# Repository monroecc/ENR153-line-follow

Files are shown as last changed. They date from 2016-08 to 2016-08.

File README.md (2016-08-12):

A simple arduino sketch to control a car (car.jpg) as it drives around a track.

control_board
--------------
Contains control board schematic files, parts list, users manual, and LaTex source files.

pid_info
--------
Contains a basic introduction to PID control and PID tuning instructions. This is a good starting point for anyone wanting to tune the PID values if the current ones aren't working out.

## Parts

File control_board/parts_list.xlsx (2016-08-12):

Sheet: Sheet1
 |  |  |  |  |  | Number of Boards: |  |  |  | 36
Parts | Website | Function | COST/unit | QTY(per board) | Cost/Board | QTY for 36 Boards | Less current inventory(not complete) | Adjusted qty | COST for 36 Boards |  | Components We may need but already have
Switch | http://www.digikey.com/product-detail/en/e-switch/500SSP1S2M2QEA/EG5137-ND/1803993 | Digital Switches | $2.61 | 3.00 | $7.83 | 108 | 0 | 108 | $281.88 |  | Wire
Header Pins(40) | http://www.digikey.com/product-detail/en/sullins-connector-solutions/PRPC040SFAN-RC/S1211EC-40-ND/2775334 | Interface with arduino and other components | $0.75 | 2.00 | $1.50 | 72 | 0 | 72 | $54.00 |  | Solder
LED's | http://www.digikey.com/product-search/en?mpart=LTL-4236N&vendor=160 | State indicator | $0.26 | 3.00 | $0.78 | 108 | 0 | 108 | $28.08 |  | Resistors
10 LED Bar | http://www.digikey.com/product-detail/en/lite-on-inc/LTA-1000G/160-1067-ND/153278 | Indicate Which sensors on line array are seeing the line | $1.30 | 1.00 | $1.30 | 36 | 0 | 36 | $46.80
QRT-8 reflectance Sensor | https://www.pololu.com/product/960 | To follow the line | $7.95 | 1.00 | $7.95 | 36 | 0 | 36 | $286.20
16 pin connector for QRT-8 | http://www.digikey.com/product-detail/en/on-shore-technology-inc/302-R161/ED10535-ND/2794246 | Connect the qrt8 sensor to the board (HEADER) | $0.42 | 1.00 | $0.42 | 36 | 0 | 36 | $15.01
16 pin (8x2) ribbon cable - 5ft | http://www.digikey.com/product-detail/en/assmann-wsw-components/AWG28-16-G-1-300-R/AE16A-5-ND/2272545 | Connect the qrt8 sensor to the board (CABLE) | $4.38 | 0.15 | $0.66 | 5.4 | 0 | 5.4 | $23.66
DCCduino uno r3 | http://www.newegg.com/Product/Product.aspx?Item=9SIA5W02EF6926 | Conroller Board - arduino uno r3 clone | $8.49 | 1.00 | $8.49 | 36 | 0 | 36 | $305.64
Connection Terminal | http://www.mouser.com/ProductDetail/TE-Connectivity/41729/?qs=EkXmzH7ytS4F3wZMq8AwJw%3D%3D | Connect board to motors | $0.23 | 2.00 | $0.46 | 72 | 0 | 72 | $16.49
9v Connector | http://www.digikey.com/product-detail/en/mpd-memory-protection-devices/BS6I-MC/BS6I-MC-ND/252231 | Connect Battery back to board | $0.69 | 1.00 | $0.69 | 36 | 36 | 0 | $0.00
5v Regulator | http://www.digikey.com/product-detail/en/fairchild-semiconductor/LM7805CT/LM7805CT-ND/458698 | Regulate voltage for arduino and servo | $0.53 | 1.00 | $0.53 | 36 | 36 | 0 | $0.00
 |  | TOTAL |  | One Board | $30.60 |  |  | For 36 Boards | $1057.76
Other Considerations
Parts | Website | consideration | COST/unit
atmega328p | http://www.digikey.com/product-detail/en/atmel/ATMEGA328P-PU/ATMEGA328P-PU-ND/1914589 | replacement microcontroller for ARDUINO uno R3, the microcontroller on the DCCduino uno can't be replaced | $3.03
arduino uno | http://www.robotshop.com/en/arduino-uno-usb-microcontroller-rev-3.html | The micro controller can be replaced, price above | $18.78
DCCduino | http://www.newegg.com/Product/Product.aspx?Item=9SIA5W02EF6926 | The micro controller can't be replaced | $8.49

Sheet: Sheet2
 |  |  |  |  |  |  |  |  | Number of Boards: |  |  |  | 100
Part | Value | Link | vendor | Part# | Function | COST/unit | QTY/Car | Cost/Car | QTY for 100 Boards | Less current inventory #(not complete)# | Adjusted qty | COST for 100 Boards |  | Components We may need but already have
Clock and Capacitors | 16MHz 18p | https://www.adafruit.com/product/2215 | DigiKey | 399-9760-ND | Provide Clock for ATMega Chip | $0.15 | 1.00 | $0.15 | 100 | 0 | 100 | $14.85 |  | Solder
Capacitor | .1u | http://www.digikey.com/product-detail/en/avx-corporation/SR215E104MAR/478-3193-ND/936835 | DigiKey | 478-3193-ND | Signal Handling | $0.14 | 3.00 | $0.41 | 300 | 0 | 300 | $41.40 |  | Flux
Capacitor | .22u | http://www.digikey.com/product-detail/en/avx-corporation/SR211E224ZAR/478-3191-ND/936833 | DigiKey | 478-3191-ND | Signal Handling | $0.17 | 1.00 | $0.17 | 100 | 0 | 100 | $16.79 |  | Multimeter
Diode | - | http://www.digikey.com/product-detail/en/fairchild-semiconductor/1N914BTR/1N914BCT-ND/458919 | DigiKey | 1N914BCT-ND | Reset Switch (See Arduino Eagle Schmatic) | $0.03 | 1.00 | $0.03 | 100 | 0 | 100 | $3.32 |  | Arduino Uno Board (1-3)
LED | - | http://www.digikey.com/product-detail/en/kingbright/WP113IDT/754-1201-ND/1747600 | DigiKey | 754-1201-ND | Indicator | $0.03 | 3.00 | $0.10 | 300 | 0 | 300 | $9.96
Switch | 4A | http://www.digikey.com/product-detail/en/e-switch/500SSP1S2M2QEA/EG5137-ND/1803993 | DigiKey | EG5137-ND | Control Volage | $2.11 | 3.00 | $6.33 | 300 | 0 | 300 | $632.70
Switch | <1A | http://www.digikey.com/product-detail/en/c-k-components/OS102011MS2QS1/CKN9542-ND/1981413 | DigiKey | CKN9542-ND | Control Volage | $0.33 | 3.00 | $0.99 | 300 | 0 | 300 | $99.46
Transistor | 2N3904 | http://www.digikey.com/product-detail/en/atmel/ATMEGA328P-PU/ATMEGA328P-PU-ND/1914589 | DigiKey | 2N3904FS-ND | Multiplex bar led output and Line sensor input | $0.09 | 1.00 | $0.09 | 100 | 0 | 100 | $9.01
Atmega Socket | 28 Pin | https://www.sparkfun.com/products/7942 | SparkFun | PRT-07942 | Holds ATMega chip, easy to replace | $0.95 | 1.00 | $0.95 | 100 | 0 | 100 | $95.00
LED Bar | 10 Segment | http://www.digikey.com/product-search/en?mpart=DC7G3HWA&vendor=754 | DigiKey | 754-1671-5-ND | Calibration and line sensor evaluation | $1.12 | 1.00 | $1.12 | 100 | 0 | 100 | $112.00
Male Pin Header | 40 Pin | https://www.sparkfun.com/products/116 | SparkFun | PRT-00116 | Misc | $1.50 | 0.33 | $0.49 | 32.5 | 0 | 32.5 | $48.75
9V Battery Clip | - | http://www.digikey.com/product-detail/en/mpd-memory-protection-devices/BS6I-MC/BS6I-MC-ND/252231 | DigiKey | BS6I-MC-ND | Connect to main power | $0.62 | 1.00 | $0.62 | 100 | 0 | 100 | $62.00
5V Regulator | LM7805 | http://www.digikey.com/product-detail/en/fairchild-semiconductor/LM7805CT/LM7805CT-ND/458698 | DigiKey | LM7805CT-ND | Provide ATMega and servo with proper votage | $0.40 | 1.00 | $0.40 | 100 | 0 | 100 | $39.65
Reflectance Sensor | QRT-8 | https://www.pololu.com/product/960 | Pololu | QTR-8A-960 | Input for line following | $6.95 | 1.00 | $6.95 | 100 | 0 | 100 | $695.00
16 Pin Angle Leads | - | http://www.digikey.com/product-detail/en/on-shore-technology-inc/302-R161/ED10535-ND/2794246 | DigiKey | ED10535-ND | Connect line sensor to board | $0.42 | 1.00 | $0.42 | 100 | 0 | 100 | $41.70
16 Pin Ribbon Cable | - | http://www.digikey.com/product-detail/en/assmann-wsw-components/AWG28-16-G-1-300-R/AE16A-5-ND/2272545 | DigiKey | AE16A-5-ND | Connect line sensor to board | $4.38 | 1.00 | $4.38 | 100 | 0 | 100 | $438.20
Reset Button | - | http://www.digikey.com/product-detail/en/cw-industries/GPTS203212B/CW182-ND/3190592 | DigiKey | CW182-ND | Reset ATMega chip | $0.61 | 1.00 | $0.61 | 100 | 0 | 100 | $61.05
 |  |  |  |  | TOTAL |  | One Board | $12.88 |  |  | For 100 Boards | $2420.84
 |  |  |  |  |  |  | One Car | $24.21
One Time Purchases
AVR Pocket Programmer | - | https://www.sparkfun.com/products/9825 | Sparkfun | PGM-09825 | Burn Bootloader | $14.95 | 2.00 | $29.90
FTDI CABLE | - | https://www.sparkfun.com/products/9718 | Sparkfun | DEV-09718 | Upload To Board | $17.95 | 2.00 | $35.90
 |  |  |  |  | TOTAL |  |  | $65.80
NOTE: | The ribbon cables are cheaper in bulk, but they must be assbled at MCC

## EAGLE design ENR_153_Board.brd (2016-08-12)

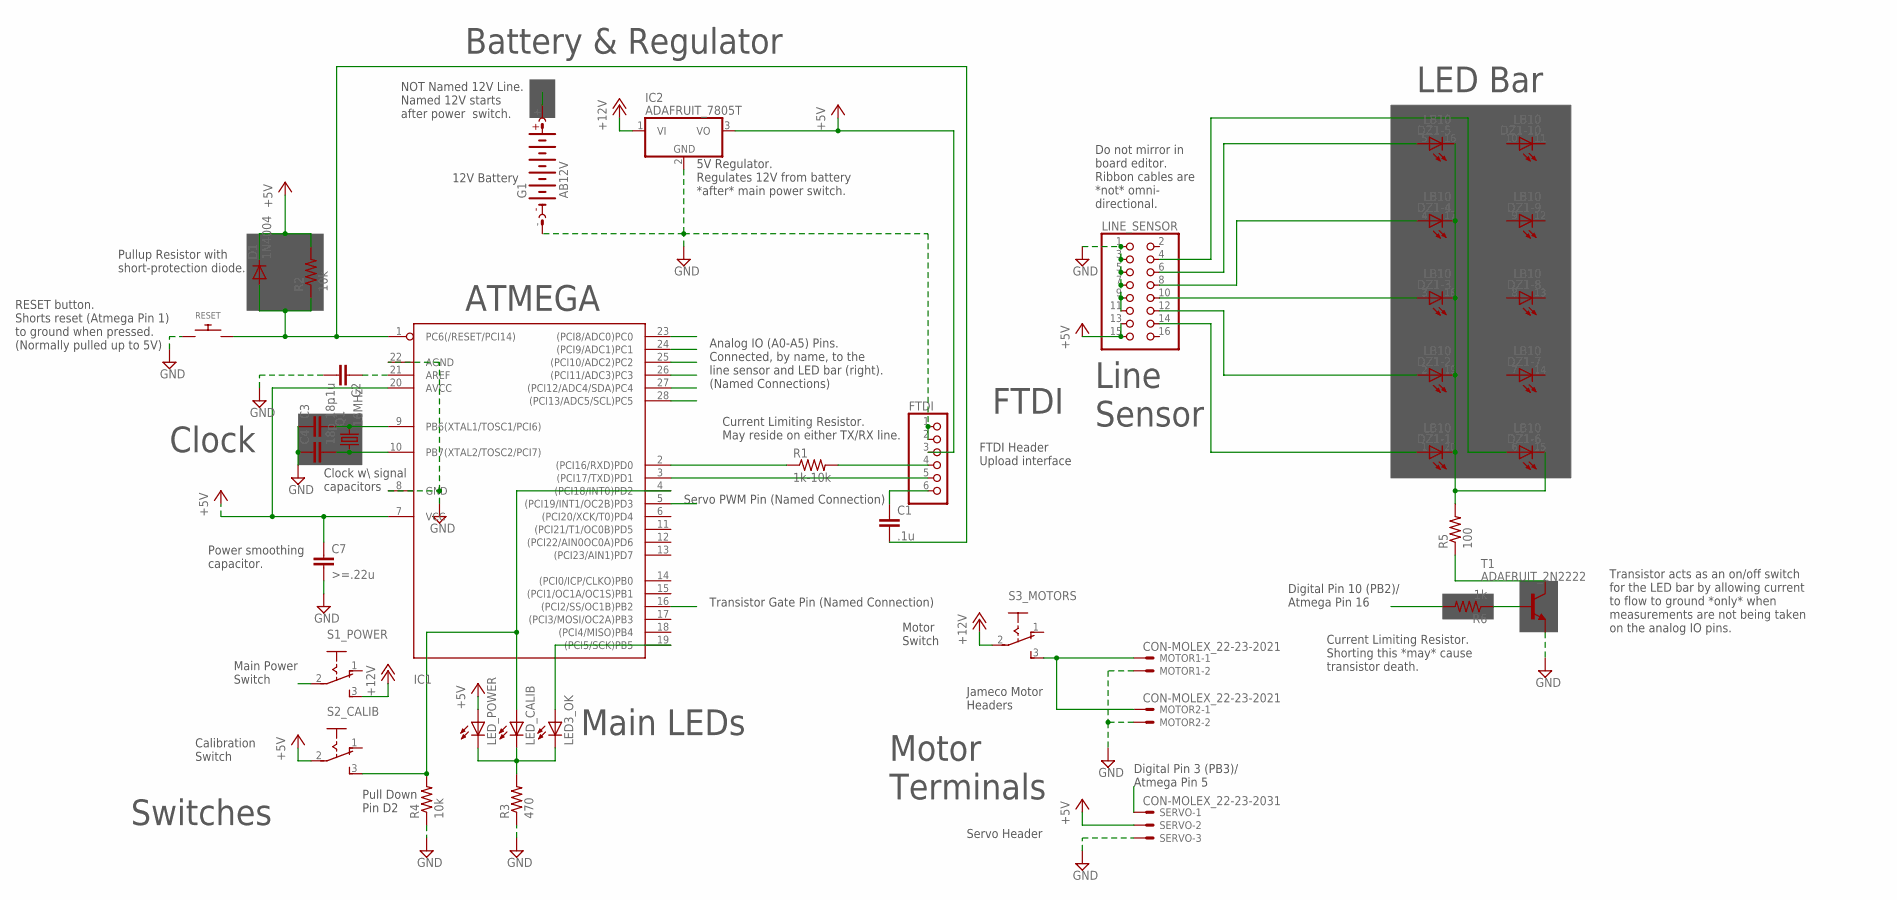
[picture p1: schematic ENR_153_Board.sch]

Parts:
C1, C2: .1u; CAPACITOR-WIMA_C5B3
C3, C4: 18p; CAPACITOR-WIMA_C5B3
C7: >=.22u; CAPACITOR-WIMA_C5B3
D1: 1N4004; DIODE_DO35-7
DZ1: LB10
FTDI: PINHD-1X6; 1X06
G1: AB12V; BATTERY_AB9V
IC1: ATMEGA168V-10P; DIL28-3
IC2: ADAFRUIT_7805T; ADAFRUIT_TO220H
LED3_OK: ADAFRUIT_LEDSQR2X5; ADAFRUIT_LED2X5
LED_CALIB: ADAFRUIT_LEDSQR2X5; ADAFRUIT_LED2X5
LED_POWER: ADAFRUIT_LEDSQR2X5; ADAFRUIT_LED2X5
LINE_SENSOR: PINHEAD_PINHD-2X8; PINHEAD_2X08
MOTOR1, MOTOR2: CON-MOLEX_22-23-2021
Q1: 16MHz; ADAFRUIT_HC49/S
R1: 1k-10k; ADAFRUIT_0207/7
R2, R4: 10k; ADAFRUIT_0207/7
R3: 470; ADAFRUIT_0207/7
R5: 100; ADAFRUIT_0207/7
R6: 1k; ADAFRUIT_0207/7
RESET: ADAFRUIT_SWITCH_PUSHBUTTONEVQ-PE; ADAFRUIT_TACT_PANA-EVQ
S1_POWER, S2_CALIB, S3_MOTORS: SWITCH_255SB
SERVO: CON-MOLEX_22-23-2031
T1: ADAFRUIT_2N2222; ADAFRUIT_TO92-EBC-OVAL

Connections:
+5V: C7.1, D1.C, FTDI.3, IC1.7 (VCC), IC1.20 (AVCC), IC2.3 (VO), LED_POWER.A, LINE_SENSOR.13, LINE_SENSOR.15, R2.2, S2_CALIB.2, SERVO.2
+12V: IC2.1 (VI), S1_POWER.3 (S), S3_MOTORS.2
A0: DZ1.6 (A), IC1.23 ((PCI8/ADC0)PC0), LINE_SENSOR.4
A1: DZ1.5 (A), IC1.24 ((PCI9/ADC1)PC1), LINE_SENSOR.6
A2: DZ1.4 (A), IC1.25 ((PCI10/ADC2)PC2), LINE_SENSOR.8
A3: DZ1.3 (A), IC1.26 ((PCI11/ADC3)PC3), LINE_SENSOR.10
A4: DZ1.2 (A), IC1.27 ((PCI12/ADC4/SDA)PC4), LINE_SENSOR.12
A5: DZ1.1 (A), IC1.28 ((PCI13/ADC5/SCL)PC5), LINE_SENSOR.14
GND: C2.2, C3.1, C4.1, C7.2, FTDI.1, FTDI.2, G1.-, IC1.8 (GND), IC1.22 (AGND), IC2.2 (GND), LINE_SENSOR.1, LINE_SENSOR.3, LINE_SENSOR.5, LINE_SENSOR.7, LINE_SENSOR.9, LINE_SENSOR.11, MOTOR1.2, MOTOR2.2, R3.1, R4.1, RESET.P$1, SERVO.3, T1.E
MAINS: G1.+, S1_POWER.2
unnamed: C1.2, D1.A, IC1.1 (PC6(/RESET/PCI14)), R2.1, RESET.P$2
unnamed: R5.1, T1.C
unnamed: FTDI.4, R1.2
unnamed: C1.1, FTDI.6
unnamed: IC1.2 ((PCI16/RXD)PD0), R1.1
unnamed: FTDI.5, IC1.3 ((PCI17/TXD)PD1)
unnamed: C2.1, IC1.21 (AREF)
unnamed: IC1.19 ((PCI5/SCK)PB5), LED3_OK.A
unnamed: LED3_OK.K (C), LED_CALIB.K (C), LED_POWER.K (C), R3.2
unnamed: C3.2, IC1.9 (PB6(XTAL1/TOSC1/PCI6)), Q1.2
unnamed: C4.2, IC1.10 (PB7(XTAL2/TOSC2/PCI7)), Q1.1
unnamed: R6.1, T1.B
unnamed: DZ1.15 (C), DZ1.16 (C), DZ1.17 (C), DZ1.18 (C), DZ1.19 (C), DZ1.20 (C), R5.2
unnamed: IC1.4 ((PCI18/INT0)PD2), LED_CALIB.A, R4.2, S2_CALIB.3 (S)
unnamed: MOTOR1.1, MOTOR2.1, S3_MOTORS.3 (S)
SERVO: IC1.5 ((PCI19/INT1/OC2B)PD3), SERVO.1
TRANSISTOR_GATE: IC1.16 ((PCI2/SS/OC1B)PB2), R6.2

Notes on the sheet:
Current Limiting Resistor. May reside on either TX/RX line.
Analog IO (A0-A5) Pins. Connected, by name, to the line sensor and LED bar (right). (Named Connections)
5V Regulator. Regulates 12V from battery *after* main power switch.
Servo Header
Jameco Motor Headers
Main Power Switch
Motor Switch
Calibration Switch
Pull Down Pin D2
LED Bar
ATMEGA
FTDI Header Upload interface
12V Battery
NOT Named 12V Line. Named 12V starts after power switch.
Power smoothing capacitor.
Current Limiting Resistor. Shorting this *may* cause transistor death.
Transistor acts as an on/off switch for the LED bar by allowing current to flow to ground *only* when measurements are not being taken on the analog IO pins.
Do not mirror in board editor. Ribbon cables are *not* omni- directional.
Digital Pin 10 (PB2)/ Atmega Pin 16
Transistor Gate Pin (Named Connection)
Servo PWM Pin (Named Connection)
Digital Pin 3 (PB3)/ Atmega Pin 5
Clock w\ signal capacitors
Pullup Resistor with short-protection diode.
RESET button. Shorts reset (Atmega Pin 1) to ground when pressed. (Normally pulled up to 5V)
Clock
Main LEDs
Switches
Line Sensor
Battery & Regulator
FTDI
Motor Terminals

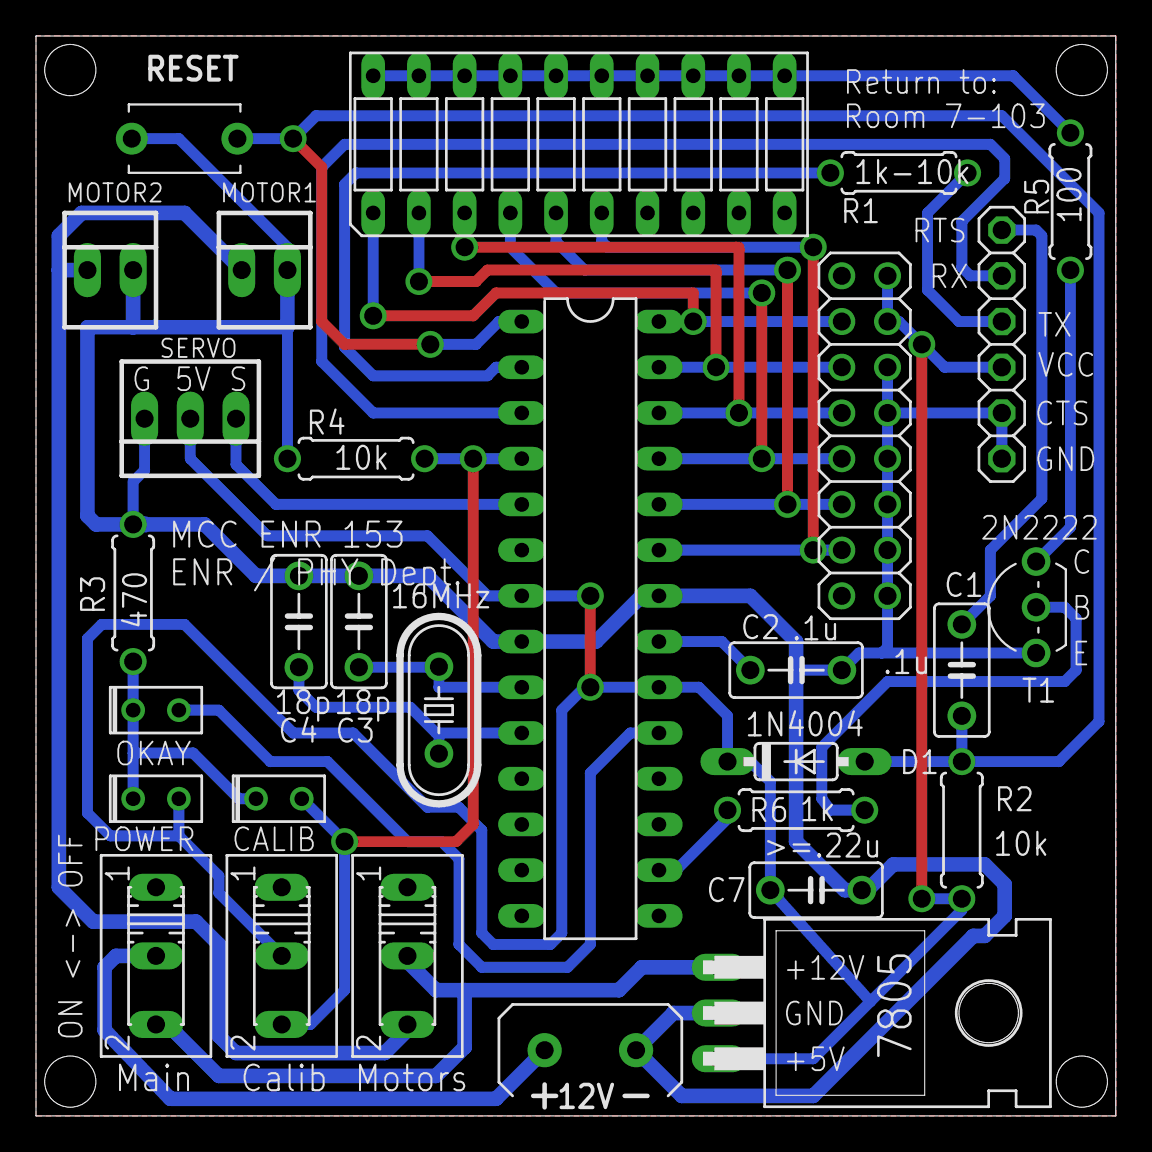
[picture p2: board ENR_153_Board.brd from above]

Board: 2 copper layers, 60.0 x 60.0 mm, 30 parts (0 on the bottom side), 27 nets.

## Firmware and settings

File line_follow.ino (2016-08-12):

#include <Servo.h>
#include "control.h"

line l;
long adjust = 5;
Servo steer;

int s_cal, state;

analog_sensor sensors[NUM_A_SENSORS];
int pin_map[NUM_A_SENSORS] = {A0, A1, A2, A3, A4, A5}; //Just incase we want to reverse the order, or in the event of a redesign adjacent sensors don't need to map to adjacent analog pins.

void setup() {
  Serial.begin(9600);
  state = -1;
  s_cal = 0;

  for (int i = 0; i < NUM_A_SENSORS; i++)
  {
    sensors[i].init(pin_map[i]);
  }

  l.init(sensors, NUM_A_SENSORS, &adjust);

  l.load();

  steer.attach(SERVO_PIN);

  pinMode(ANALOG_TRANSISTOR_PIN, OUTPUT);
  digitalWrite(ANALOG_TRANSISTOR_PIN, LOW);
}


void loop() {

  if ((millis() % 100) < 5) //Only check every 100ms. Makes loop faster assuming digitalRead() is slower than logical condition
    s_cal = digitalRead(CALIBRATE_PIN);

  switch (state)
  {
    case 0:
      l.follow();
      adjust = constrain(adjust, MAX_ADJ_RIGHT, MAX_ADJ_LEFT);
      steer.write(SERVO_CENTER - adjust);
      state = s_cal;
      break;
    case 1:
      l.clear_calibration();
      steer.write(SERVO_CENTER);
      state = 2;
      break;
    case 2:
      l.calibrate();
      display_line(l);
      if (s_cal == LOW)
        state = 3;
      break;
    case 3:
      l.save();
      state = 0;
      break;
    default:
      state = 0;
  }
}

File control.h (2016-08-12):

#ifndef CONTROL
    #define CONTROL

    #include "definitions.h"

    //#define DEBUG       // Uncommenting this line prints the binary representation of the line sensor to the console during calibration
    //#define DEBUG_EACH  // Uncommenting this line prints the min and max line sensor values to the console during calibration

    #ifdef DEBUG
        #include "toolbox.h" //debug tools
    #endif

    #define NUM_A_SENSORS 6             // Number of analog sensors, used as array length
    #define CALIBRATE_PIN 2             // Connected to the calibration pin
    #define ANALOG_TRANSISTOR_PIN 10    // Pin connected to the transistor base, used to cut the bar led out of the line follow circuit
    #define SERVO_PIN 3                 // Servo is connected to this pin, it is a PWM pin
    
    #include <Arduino.h>
    #include <EEPROMex.h> //Make sure you install this via the Arduino IDE, allows writing of things other than bytes

    //GENERAL PID
    class PID
    {
    public:
        float pidd[4]; //err, last error, running integral, adjust
        float w[3];    //holds pid constants

        float circ_i[I_BUFFER_LEN]; // only worry about summing the last 30 terms of remond sum
        int head;         // head for circuilar array

        void set_pid(float p, float i, float d)
        {
            w[0] = p;w[1] = i;w[2] = d;
            pidd[0] = 0; pidd[1] = 0; pidd[2] = 0;
            head = 0;

            memset(circ_i, 0x00, sizeof(float)*I_BUFFER_LEN);
        }

        float slice(float err)
        {
            pidd[1] = pidd[0];                      // set last err pidd[1]
            pidd[0] = err;                          // set current err pidd[0]

            //The integral term only takes into account the last I_BUFFER_LEN readings. It only sums these readings when the car is moving away from the line. When moving towards the line the integral term is set to zero along with the circular buffer.
            if( abs(pidd[0]) > abs(pidd[1]) ){
                pidd[2] -= circ_i[head];                // Subract off the element of circ_i you are about to replace
                circ_i[head] = (pidd[0] + pidd[1])/2;   // Set the element of the cirular array to this "slice" of the integral
                pidd[2] += circ_i[head];                // Add to integral element pidd[2]
                head++;                                 // increments head

                if(head == I_BUFFER_LEN)
                    head = 0; //wrap around

            }else if(circ_i[head] != 0.0){
                //only clear the buffer once, readings of zero pretty much never happen
                pidd[2] = 0;
                memset(circ_i, 0x00, sizeof(float)*I_BUFFER_LEN); // clear buffer
            }                             


            pidd[3] = pidd[0]*w[0] + pidd[2]*w[1] + (pidd[0] - pidd[1]) * w[2]; // Compute PID output and save it in pidd[3]

            return pidd[3];                                                     // return adjustment
        }
    };

    class analog_sensor
    {
    public:
        int pin, min, max; //analog pin [0, 5], absolute min for this sensor, absolute max for this sensor
        float scale;      // Scale value, used to fit any reading to a value between 0-100 (normalize sensor)
        static int eeprom_head; // The current eeprom position, keeps sensors from overwriting each others calibration
        void init(int arg_pin)
        {
            this->pin = arg_pin;
            this->scale = 1.0;
            this->min = 2000;
            this->max = 0;
        }

        int read_sensor()
        {
            // Nomalize sensor, contrain, and return
            int ret = (int)((analogRead(pin) - min)*scale); //calculate normalized sensor value
            ret = constrain(ret, 0, 100);
            return ret;
        }

        void calibrate_point()
        {
            int cal = analogRead(pin);
            if(cal < min){
                min = cal; // Set new absolute min
            }
            else if(cal > max){
                max = cal;  // Set new absolute max
            }
            scale = 100.0/(max - min);  // Compute scale
        }

        static void reset_head()
        {
            analog_sensor::eeprom_head = EEPROM_OFF;
        }

        void reset_calibration()
        {
            this->scale = 1.0;
            this->min = 1025;
            this->max = 0;
        }

        void save() //save cailbration (min, max) for this sensor
        {
            EEPROM.writeInt(eeprom_head, min);
            eeprom_head += sizeof(int);
            EEPROM.writeInt(eeprom_head, max);
            eeprom_head += sizeof(int);
        }

        void load() //load calibration for this sensor
        {
            min = EEPROM.readInt(eeprom_head);
            eeprom_head += sizeof(int);
            max = EEPROM.readInt(eeprom_head);
            eeprom_head += sizeof(int);

            scale = 100.0/(max - min);
        }
    };

    int analog_sensor::eeprom_head = 0;

    class line
    {
    private:
        analog_sensor * sensors;    // Array of sensors to compute line position from
        PID pidlf;                  
        int nsensors, last_line;    // number of sensors, last_line is the last place the sensor saw the line, either 0 (left) or 1 (right)
        long * adjust;              // pointer to variable to be adjusted by pid
        long w, wsum, pos;          //weights, weighted sum, position on line
        char linechar;              //character representation of line
        char flag;                  //a flag
    public:
        void init(analog_sensor * a_sensors, int len, long * adj)
        {
            pidlf.set_pid(P, I, D); //set pid values, TODO: this should be somewhere else
            adjust = adj;
            sensors = a_sensors;
            nsensors = len;
            this->read_line();
            flag = 0;
            last_line = 1;
        }

        void clear_calibration() //everytime the car enters calibrate mode the previous calibration is erased
        {
            for (int i = 0; i < nsensors; ++i)
            {
                sensors[i].reset_calibration();
            }
        }

        void calibrate()
        {
            for (int i = 0; i < nsensors; ++i)
            {
                //reads the sensor once and incoperates that into the calibration
                sensors[i].calibrate_point();
            }
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

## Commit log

2016-07-28 works, pid needs tuning
2016-07-29 tuned PID, added definitions file
2016-08-11 Added Eagle files
    [ENR153_control_board.brd, ENR153_control_board.sch]
2016-08-12 added pdf's for pid, more comments
2016-08-12 added parts list, manual, and latex source (zip)
    [parts_list.xlsx]
2016-08-12 Added Finalized Board and Schematic Files.
    [ENR_153_Board.brd, ENR_153_Board.sch]
